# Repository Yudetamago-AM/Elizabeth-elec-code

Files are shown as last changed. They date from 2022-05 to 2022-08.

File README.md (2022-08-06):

# CanSat2022

この文書をソフト全体のドキュメントとして扱えるようにしたいなーと思っています．

## 注意
プログラムを書く前に，VS Codeのソース管理タブ→三点リーダ，レポジトリからプルすること．

## はじめに

ここでは，第18回能代宇宙イベントに向けた缶サットのプログラムを開発する．なお，われわれの缶サットの成功基準は下のように定められている．

| 種別 | 基準 |
| ---- | ---- |
| Minimum Success | 機体の損傷無く着地し，パラシュートを切り離す．制御履歴を保存する． |
| Full Success | 正常な動作を開始し，ゴール5m圏内に近づく． |
| Extra Success | ゴール0mまで近づき停止する． |

## 本番の流れ

1. 前日にゴール場所の座標を調べる．
1. 当日投下前に，動作タイマーをセットする．
1. 投下→自動誘導
この中で使うプログラムをここで書いていく．

## 回路について

### 搭載部品

主要な搭載部品は以下の通りである．

| 役割 | 型番 | 参考になるサイト |
| --- | --- | --- |
| マイコン | ATmega328P | <https://ht-deko.com/arduino/atmega328p.html> |
| GNSS | AE-GYSFDMAXB | <https://github.com/askn37/GPS_MTK333X> |
| 9軸センサー | AE-BNO055-BO | <https://learn.adafruit.com/adafruit-bno055-absolute-orientation-sensor/arduino-code> |
| 超音波距離センサー | HC-SR04 | <https://akizukidenshi.com/catalog/g/gM-11009/> |
| microSD | AE-microSD-LLCNV | <https://akizukidenshi.com/catalog/g/gK-14015/> |
| モータードライバ | TB67H450FNG | <https://www.marutsu.co.jp/contents/shop/marutsu/datasheet/TB67H450FNG.pdf> |

なお，マイコンと部品間のピンアサインは，PinAssign.hを参照．

## 実装上の注意

メモリが限られている（全体で2048バイト，SDカードのバッファ用に512バイト，Arduino Bootloaderにいくらか持って行かれている）ため，メモリを節約してプログラムを書くこと．

## 必要なライブラリ

### モーター制御

がんばって書く，TB67H450FNGを用いたPWM定電流制御．電流値は，基板上の抵抗で決める．
前進，後進，ブレーキ，超信地旋回ができるように．早さはPWMで指定して呼び出す感じにする．
PWMは100以上くらいじゃないと，うまく回らない印象（実際に使うモーターでなくて，マブチモーターだけど）．あと，回り始めに一気に電流が必要そうなので，コンデンサの容量増やしたりした方が良いかも．

### GNSS情報取得

<https://github.com/askn37/GPS_MTK333X>
このなんだか便利（シンプル）そうなライブラリが使えそうです．なので，ちょちょっとメイン制御の方に書くのみで大丈夫と思います．

### ログ記録

AE-microSD-LLCNVを使う．がんばって書く．そんなに大変そうじゃ無い．

### 9軸

方位，加速度などを取得する．秋月のBNO055採用のため，Adafruitのライブラリが使える．
方位の値が安定しない問題があったが，SDAに2.2K, SCLに3.3Kのプルアップ抵抗を付けることで解決する（詳細はAdafruit BNO055のFAQを参照）．
→組み立て時に追加する．
また，信頼できる値は，bno.getCalibration(引数)の相当する引数の値が，0でない時である．

## メインプログラム

### メイン制御 [Main.ino]

各Seqをそれぞれ呼び出す．

### Landing()

- 着地判定
9軸の加速度の大きさ，（GPSの速度の大きさを見る），念のためタイマーも入れておく．
- パラシュートに絡まないようにする（すこし前に進む？）．
- ニクロム線カット
PIN_NICHROME(中身はanalog pin 7(PD7))をHIGHにすればオンになるはず．

#### ニクロム線溶断について

実験してみたところ，ニクロム線が短すぎると，バッテリの短絡防止回路がうごいて，モーター・ニクロム線系統の電源が落ちてしまう．
ニクロム線を長めに取る（5Ω分くらい）と，うまくいく（抵抗を付けるのもありかも→要実験）．
溶断にかかる時間は，ある程度テンションをかけた状態で，3秒ほどであった．
このため，ニクロム線の長さにもよるが，5秒ほど電流を流した方が良いかと思う．

### GuideGPS()

- GPSで精度限界まで誘導する
上に上げたライブラリを叩いて今の座標とか取得して良い感じに計算して誘導すれば良いはず．

今更気付いたのだが，Arduinoのfloat型は"the total number of digits"で6-7桁しか精度がないため，目的地への角度・距離の計算結果には十分な精度がない（というのも，緯度・経度は小数点以下6桁でおよそ10cm精度が出るためであり，われわれにはこのくらい必要だからである）．
困ったので，GPSの座標は固定小数点として扱う．

### GuideDIST()

- 超音波距離センサーで0mまで誘導する

われわれはついてるはずなので，カラーコーン±50cmくらいまでGPSで誘導できるはず．その後，超信地旋回をしながら，カラーコーンの位置と距離を認識して，その距離分進む．

### Goal()

ゴール判定をする．ゴールと判定したら，プログラム終了！
GuideDIST()でむしろ明後日の方向へ行ってしまっているようならば，もういちどGPSで誘導して終わりにする．

### Distance()

超音波距離センサーをつかって，目の前の物体までの距離をcmで返す．
（一応，九軸センサー内の温度センサーをつかって音速を校正しているが，逆に安定性を損なうようだったら，→board tempなのか…ならばつかえないのか）20℃1気圧とかで計算しておく．

### タイマー [Main.ino]

あらかじめ設定してあるタイマー（int Timer）(ms)と，millis()を比較する．
（millis()はプログラム開始からの時間をmsで返す）（<http://www.musashinodenpa.com/arduino/ref/index.php?f=0&pos=2524>）

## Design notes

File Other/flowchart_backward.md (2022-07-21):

#
```flow

start=>start: 開始
end=>end: 終了

getrad=>operation: 機体のピッチ取得
forward=>operation: モーター制御
（前転）
isbackward=>condition: 機体が
反転しているか
log=>operation: ログ書き込み

start->getrad(right)->isbackward(no, bottom)->log(right)->end
isbackward(yes)->forward(right)->log

```

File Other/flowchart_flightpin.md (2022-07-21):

```flow

start=>start: 開始
end=>end: 終了

flightpin=>condition: フライトピン

```

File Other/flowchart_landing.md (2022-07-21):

```flow

start=>start: 開始
end=>end: 終了
flightPin=>condition: フライトピン解放
からの時間 > 40(s)
timer=>condition: 電源投入からの
時間 > 600(s)
cutting=>subroutine: テグス溶断
log=>operation: ログ書き込み
phase=>operation: フェーズ=GPS誘導フェーズ

start->flightPin(yes)->cutting
flightPin(no)->timer
timer(no)->flightPin()
timer(yes)->cutting(right)->log(right)->phase->end

```

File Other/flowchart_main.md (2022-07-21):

```flow

start=>start: 開始
end=>end: 終了
wait=>subroutine: フライトピン
landing=>subroutine: 着地時動作
gpsGuide=>subroutine: GPS誘導
distGuide=>subroutine: 精密誘導
isGoal=>condition: ゴール判定
timesCalled=>condition: 呼出回数 < 3
 
start->wait->landing->gpsGuide->timesCalled

```

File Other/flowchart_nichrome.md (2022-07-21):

##

```flow

start=>start: 開始
end=>end: 終了
Nichrome=>operation: ニクロム線加熱
（テグス溶断）
forward=>operation: モーター制御
（前進）

start(right)->Nichrome(right)->forward(right)->end

```

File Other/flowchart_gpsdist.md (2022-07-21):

```flow

start=>start: 開始
end=>end: 終了
backward=>subroutine: 機体の反転検出・修正
rotate90=>operation: 90度左旋回
rotate=>operation: 10度右旋回
checkdist=>inputoutput: 前方の距離確認
ischecked=>condition: 物体検知したか
rotatedir=>operation: 物体の方向へ旋回
forward=>operation: モーター制御
（直進）
log=>operation: ログ書き込み
isgoal=>operation: フェーズ=ゴール判定フェーズ

start->backward->rotate90->checkdist->rotate->ischecked
ischecked(yes)->rotatedir->forward->log->isgoal->end
ischecked(no)->checkdist

```

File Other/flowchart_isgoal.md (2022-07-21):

```flow

start=>start: 開始
end=>end: 終了
end2=>end: 終了

backward=>subroutine: 機体の反転検出・修正
gpscheck=>operation: ゴールまでの距離・方位取得
dist400=>condition: ゴールまでの
距離 < 400(cm)
goalcount=>condition: ゴール判定の
呼出回数 < 5
distfor=>inputoutput: 機体前側の距離取得
distfor2=>inputoutput: 機体前側の距離取得
rotate=>operation: 小旋回
phasegps=>operation: フェーズ=GPS誘導
phasedist=>operation: フェーズ=精密誘導
phase5=>operation: フェーズ=回収まで待機
phase5b=>operation: フェーズ=回収まで待機
log=>operation: ログ書き込み
log2=>operation: ログ書き込み
check=>condition: 距離 < 12(cm)
calcgps=>subroutine: ゴールへの方位・距離計算

start(right)->backward(right)->calcgps->dist400
dist400(no)->goalcount
dist400(yes, right)->phasegps->phase5->log->end2
goalcount(no)->phasegps
goalcount(yes, right)->distfor->check
check(yes)->log2->phase5b->end
check(no)->phasedist->phase5b

```

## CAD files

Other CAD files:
Experiments/PlainC_gpsCalc/GPScalc.obj

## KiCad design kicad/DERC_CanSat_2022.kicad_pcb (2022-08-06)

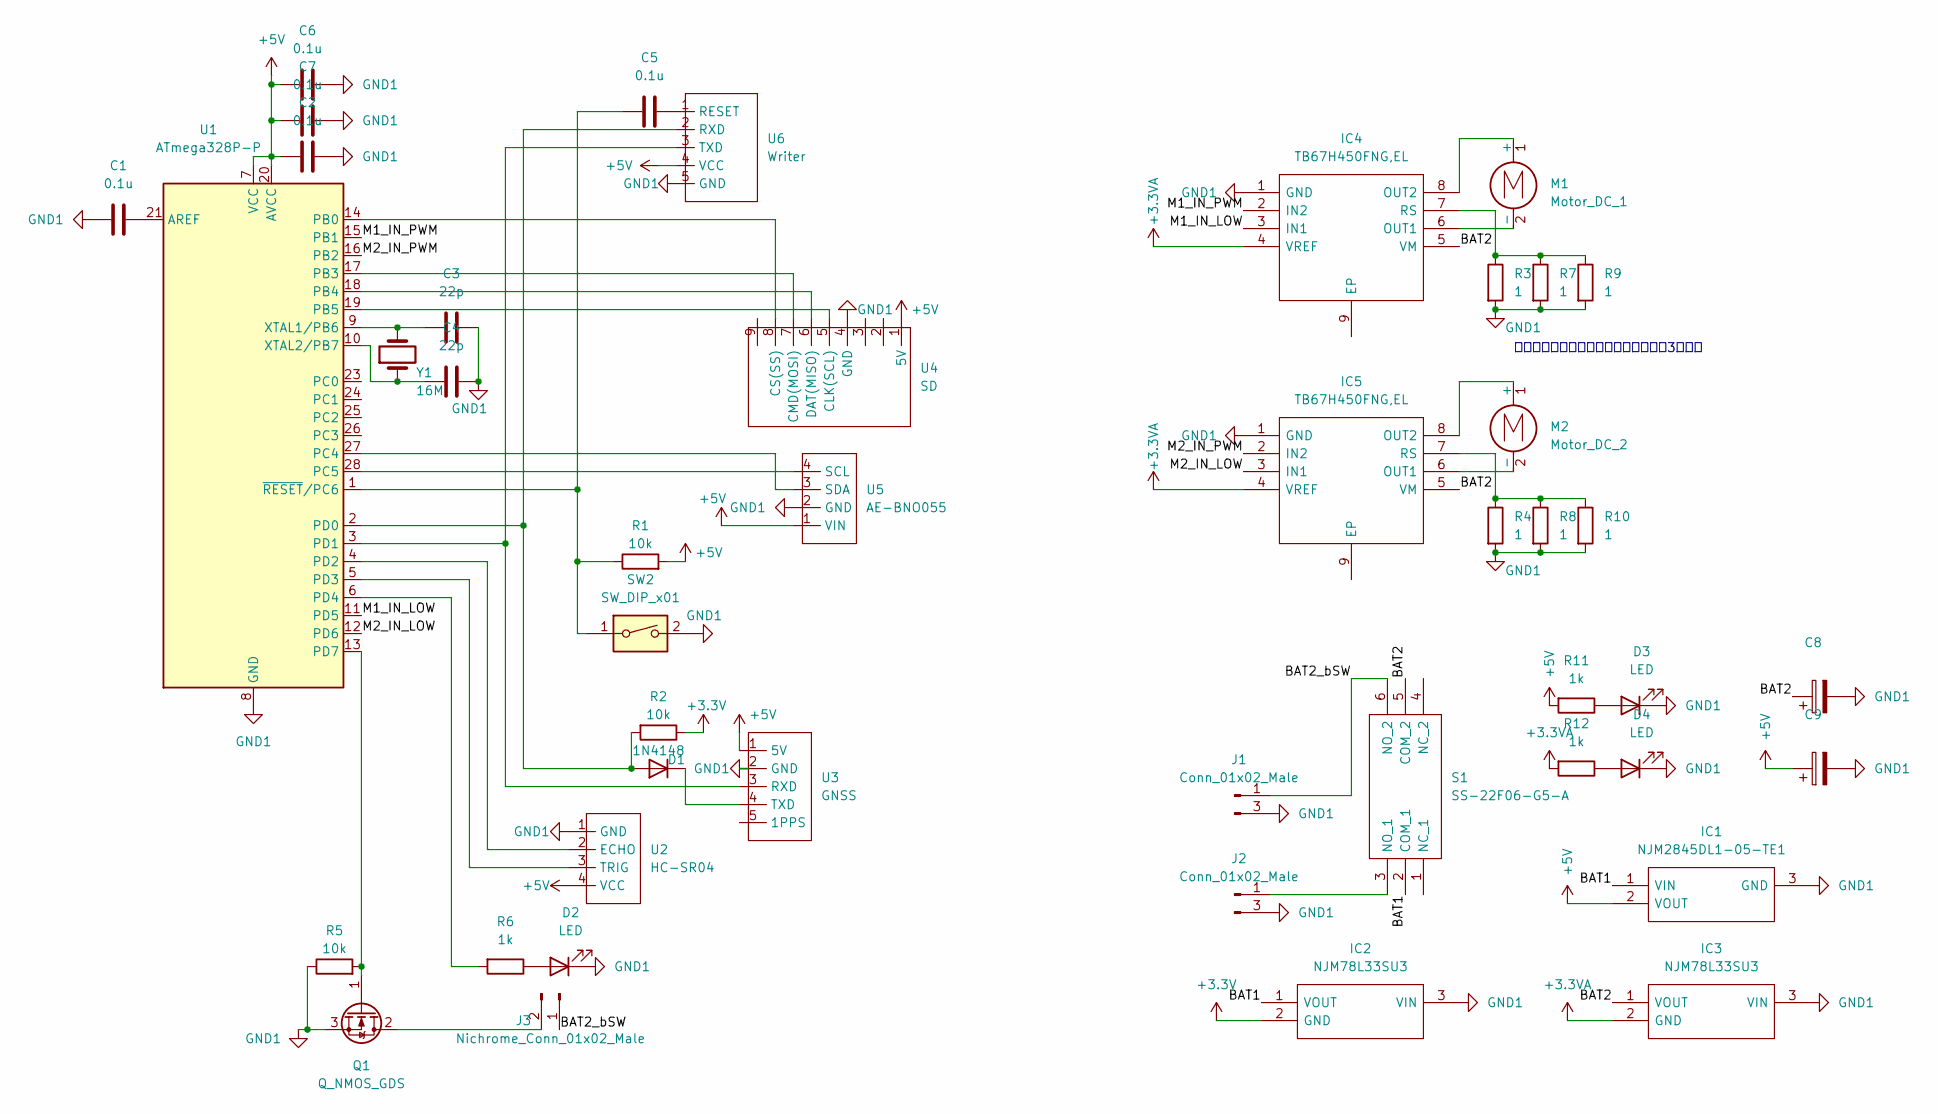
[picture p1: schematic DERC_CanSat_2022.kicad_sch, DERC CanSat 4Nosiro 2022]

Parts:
C1, C2, C5, C6, C7: 0.1u; C_Disc_D3.0mm_W1.6mm_P2.50mm
C3, C4: 22p; C_Disc_D3.0mm_W1.6mm_P2.50mm
C8, C9: (no value)
D1: 1N4148; D_DO-35_SOD27_P7.62mm_Horizontal
D2, D3, D4: LED; LED_D3.0mm
IC1: NJM2845DL1-05-TE1; TO-252-2; Manufacturer_Part_Number NJM2845DL1-05-TE1
IC2, IC3: NJM78L33SU3; SOT-89-3; Manufacturer_Part_Number NJM78L33SU3
IC4, IC5: TB67H450FNG,EL; SOIC127P600X175-9N; Manufacturer_Part_Number TB67H450FNG,EL
J1, J2: Conn_01x02_Male; JST_PH_B3B-PH-K_1x03_P2.00mm_Vertical
J3: Nichrome_Conn_01x02_Male; TerminalBlock_Altech_AK300-2_P5.00mm
M1: Motor_DC_1; JST_XH_B2B-XH-A_1x02_P2.50mm_Vertical
M2: Motor_DC_2; JST_XH_B2B-XH-A_1x02_P2.50mm_Vertical
Q1: Q_NMOS_GDS; TO229P241X654X988-3P
R1, R2, R5: 10k; R_Axial_DIN0207_L6.3mm_D2.5mm_P7.62mm_Horizontal
R3, R4, R7, R8, R9, R10: 1; R_Axial_DIN0207_L6.3mm_D2.5mm_P2.54mm_Vertical
R6, R11, R12: 1k; R_Axial_DIN0207_L6.3mm_D2.5mm_P7.62mm_Horizontal
S1: SS-22F06-G5-A; PowerSwitch; Manufacturer_Part_Number SS-22F06-G5-A
SW2: SW_DIP_x01; TVBP06B043CWB
U1: ATmega328P-P; DIP-28_W7.62mm
U2: HC-SR04
U3: GNSS
U4: SD
U5: AE-BNO055
U6: Writer; PinHeader_1x05_P2.54mm_Vertical
Y1: 16M; Crystal_HC49-4H_Vertical

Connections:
+3.3VA: IC3.2 (GND), IC4.4 (VREF), IC5.4 (VREF), R12.2
+3V3: IC2.2 (GND), R2.1
+5V: C2.1, C6.1, C7.1, C9.1, IC1.2 (VOUT), R1.2, R11.2, U1.7 (VCC), U1.20 (AVCC), U2.4 (VCC), U3.1 (5V), U4.1 (5V), U5.1 (VIN), U6.4 (VCC)
/BAT1: IC1.1 (VIN), IC2.1 (VOUT), S1.2 (COM_1)
/BAT2: C8.1, IC3.1 (VOUT), IC4.5 (VM), IC5.5 (VM), S1.5 (COM_2)
/BAT2_bSW: J1.1, J3.1, S1.6 (NO_2)
/M1_IN_LOW: IC4.3 (IN1), U1.11 (PD5)
/M1_IN_PWM: IC4.2 (IN2), U1.15 (PB1)
/M2_IN_LOW: IC5.3 (IN1), U1.12 (PD6)
/M2_IN_PWM: IC5.2 (IN2), U1.16 (PB2)
GND1: C1.1, C2.2, C3.2, C4.2, C6.2, C7.2, C8.2, C9.2, D2.1 (K), D3.1 (K), D4.1 (K), IC1.3 (GND), IC2.3 (VIN), IC3.3 (VIN), IC4.1 (GND), IC5.1 (GND), J1.3 (Pin_2), J2.3 (Pin_2), Q1.3 (S), R3.2, R4.2, R5.1, R7.2, R8.2, R9.2, R10.2, SW2.2, U1.8 (GND), U1.22 (GND), U2.1 (GND), U3.2 (GND), U4.4 (GND), U5.2 (GND), U5.6, U6.5 (GND)
unnamed: C1.2, U1.21 (AREF)
unnamed: C3.1, U1.9 (XTAL1/PB6), Y1.2
unnamed: C4.1, U1.10 (XTAL2/PB7), Y1.1
unnamed: C5.1, R1.1, SW2.1, U1.1 (~RESET/PC6)
unnamed: C5.2, U6.1 (RESET)
unnamed: D1.1 (K), U3.4 (TXD)
unnamed: D1.2 (A), R2.2, U1.2 (PD0), U6.2 (RXD)
unnamed: D2.2 (A), R6.1
unnamed: D3.2 (A), R11.1
unnamed: D4.2 (A), R12.1
unnamed: IC4.6 (OUT1), M1.2 (-)
unnamed: IC4.7 (RS), R3.1, R7.1, R9.1
unnamed: IC4.8 (OUT2), M1.1 (+)
unnamed: IC5.6 (OUT1), M2.2 (-)
unnamed: IC5.7 (RS), R4.1, R8.1, R10.1
unnamed: IC5.8 (OUT2), M2.1 (+)
unnamed: J2.1, S1.3 (NO_1)
unnamed: J3.2, Q1.2 (D)
unnamed: Q1.1 (G), R5.2, U1.13 (PD7)
unnamed: R6.2, U1.6 (PD4)
unnamed: U1.3 (PD1), U3.3 (RXD), U6.3 (TXD)
unnamed: U1.4 (PD2), U2.2 (ECHO)
unnamed: U1.5 (PD3), U2.3 (TRIG)
unnamed: U1.14 (PB0), U4.8 (CS(SS))
unnamed: U1.17 (PB3), U4.7 (CMD(MOSI))
unnamed: U1.18 (PB4), U4.6 (DAT(MISO))
unnamed: U1.19 (PB5), U4.5 (CLK(SCL))
unnamed: U1.27 (PC4), U5.3 (SDA)
unnamed: U1.28 (PC5), U5.4 (SCL)

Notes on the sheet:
抵抗値で定電流制御の電流決めるため3本パラ

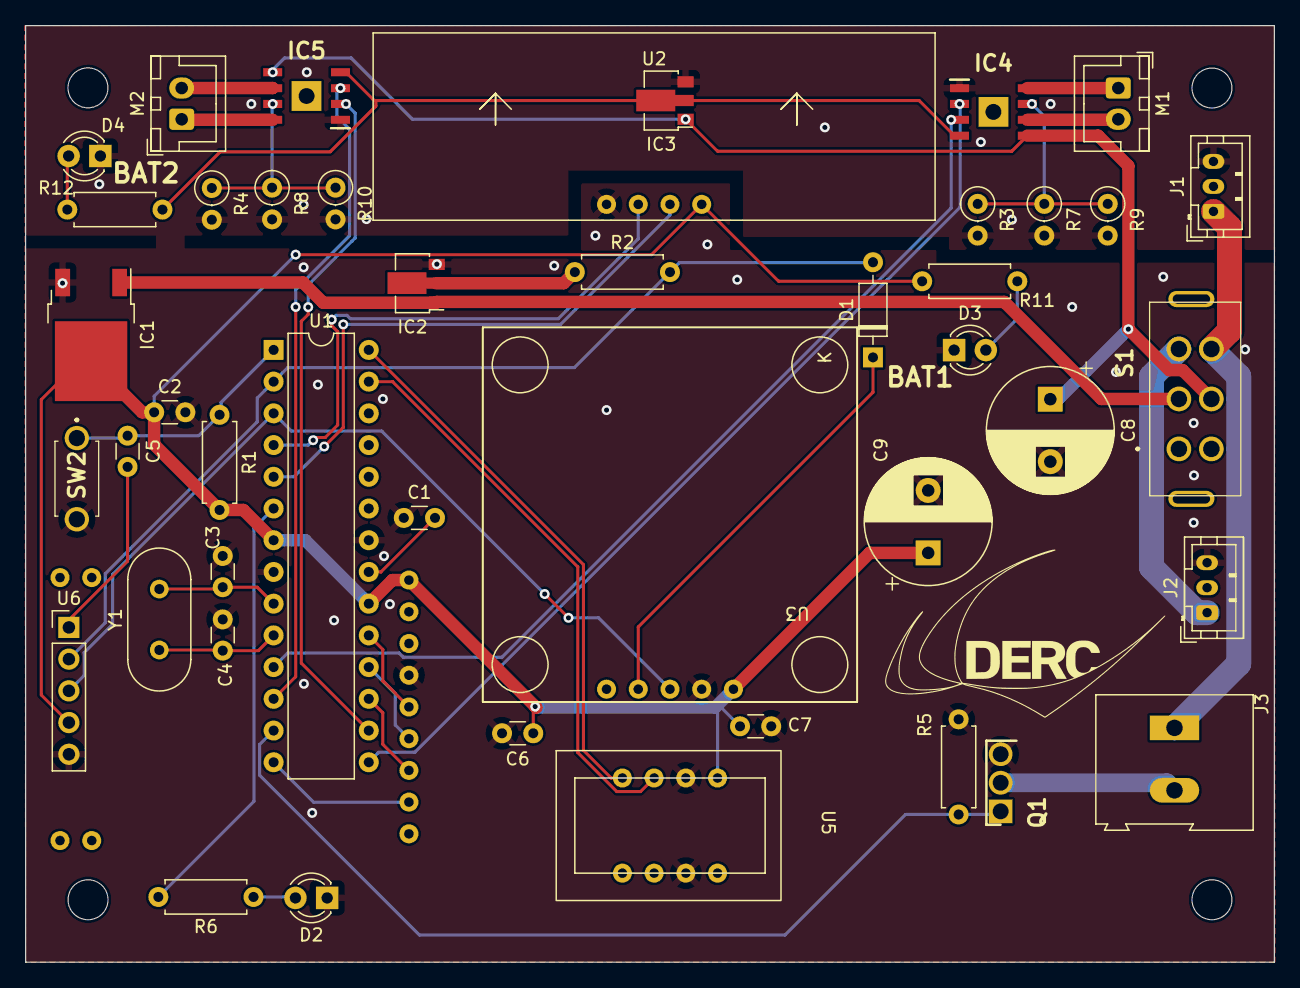
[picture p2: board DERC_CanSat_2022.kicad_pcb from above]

Board: 2 copper layers, 100.0 x 75.0 mm, 46 parts (1 on the bottom side), 40 nets.

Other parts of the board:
2022: LOGO; logotekina_25

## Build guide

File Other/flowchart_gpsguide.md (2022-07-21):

```flow

start=>start: 開始
end=>end: 終了

backward=>subroutine: 機体の反転検出・修正
getgps=>inputoutput: GPS座標取得
getrad=>inputoutput: 機体の方位取得
calcgps=>subroutine: ゴールへの方位・距離計算
rotate=>operation: モーター制御（旋回）
log=>operation: ログ書き込み
isdone=>condition: ゴールまでの
距離 < 3m
phase=>operation: フェーズ=精密誘導フェーズ

start->backward->calcgps()->rotate->log->isdone
isdone(yes, right)->phase->end
isdone(no)->end

```

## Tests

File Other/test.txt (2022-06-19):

set datafile separator ","
set yrange [-40: 40]
set xlabel "Time (ms)"
set ylabel "Accel (m/s^2)"
plot "L14.dat" using 1:2 w lp title "X-axis"
replot "L14.dat" using 1:3 w lp title "Y-axis"
replot "L14.dat" using 1:4 w lp title "Z-axis"

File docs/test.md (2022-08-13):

# テスト

これはテストファイルです．

>We look before and after  \
>　　And pine for what is not:  \
>Our sincerest laughter  \
>　　With some pain is fraught;  \
>Our sweetest songs are those that tell of saddest thought.

>「前をみては、後えを見ては、物欲しと、あこがるるかなわれ。腹からの、笑といえど、苦しみの、そこにあるべし。うつくしき、極の歌に、悲しさの、極みの想、籠るとぞ知れ」

（夏目漱石『草枕』より．
青空文庫：<https://www.aozora.gr.jp/cards/000148/files/776_14941.html>）

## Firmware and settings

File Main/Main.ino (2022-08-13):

/*
あらかじめ，
https://github.com/askn37/Futilities
https://github.com/askn37/GPS_MTK333X
https://github.com/adafruit/Adafruit_Sensor
https://github.com/adafruit/Adafruit_BusIO
https://github.com/adafruit/Adafruit_BNO055
をライブラリに読み込んでおくこと．
*/

#include <Arduino.h>
#include <Wire.h>
#include <SoftwareSerial.h>
#include <GPS_MTK333X_SoftwareSerial.h>
//#include <GPS_MTK333X_Serial.h>
#include <Adafruit_Sensor.h>
#include <Adafruit_BNO055.h>
#include <utility/imumaths.h>
/*以下lib内自作ライブラリ*/
#include <PinAssign.h>
#include <Motor.h>
#include <SD_RW.h>

#define ANGLE_TH 0.39//前45度，GPS誘導
#define LONGITUDE_PER_RES 141//能代
#define LATITUDE_PER_RES 185

byte phase = 0;
/*重要！！電源オンからのタイマー，ミリ秒単位で指定*/
const unsigned long Timer = 600000; //600 * 1000, 600秒 は 10分
/*フライトピン解放からのタイマー*/
const unsigned int flightPinTimer = 10000;//50s//10s
unsigned long flightPinMillis;
/*重要！！ゴールのGPS座標*/
const long goal_longitude = 84082711; //経度*600000(60万)
const long goal_latitude = 24135694; //緯度*600000

bool isFirstUnplug = true;
bool isFirstDIST = false;
byte goalCount = 0;

GPS_MTK333X_SoftwareSerial GPS(PIN_GPS_RX, PIN_GPS_TX);
//GPS_MTK333X_Serial GPS;
Adafruit_BNO055 bno = Adafruit_BNO055(55, 0x28);

void setup() {
    /*Motor initialize*/
    motor_init();
    motor_stop();

    /*ニクロム線の初期設定*/
    pinMode(PIN_NICHROME, OUTPUT);
    digitalWrite(PIN_NICHROME, LOW);

    /*//Serial (for debug) initialize*/
    Serial.begin(9600);
    Serial.println(F("Serial begin"));

    /*FOR DEBUG!! mem check*/
    /*不要なときはコメントアウト！！*/
    // 5/16時点で723bytesあまってる感じ
    /*
    //Serial.print(F("Free memory="));
    //Serial.print(freeRam(), DEC);
    //Serial.println(F("[bytes]"));
    */

    /*SD initialize*/
    sd_init();

    /*BNO055 initialize*/
    while (!bno.begin()) {
        //Serial.println(F("BNO055 not ready"));
        delay(100);
    }
    bno.setExtCrystalUse(true);//のっかってるからには使わねば（精度向上）
    //Serial.println(F("BNO055 ready"));

    /*GPS initialize*/
    while (!GPS.begin(9600)) {
        //Serial.println(F("GPS not ready"));
        delay(100);
    }
    // UARTボーレートを 9600bpsに設定する
    GPS.sendMTKcommand(251, F(",9600"));
    // 1000ms間隔で NMEAを出力する
    GPS.sendMTKcommand(220, F(",1000"));
    //GPS.sendMTKcommand(300, F(",1000,0,0,0,0"));
    // AlwaysLocate モード開始 
    //GPS.sendMTKcommand(225, F(",8"));
    // 上記を解除してスタンダードモードに遷移
    GPS.sendMTKcommand(225, F(",0"));
    // QZSS（みちびき）をサポートする
    GPS.sendMTKcommand(351, F(",1"));
    // RMCとGGAをともに1サイクルで出力する（1サイクル時間は PMTK220 による）
    // 各項は ",GLL,RMC,VTG,GGA,GSA,GSV,0,0,0,0,0,0,0,0,0,0,0,ZDA,MCHN"
    GPS.sendMTKcommand(314, F(",0,1,0,1,0,0,0,0,0,0,0,0,0,0,0,0,0,0,0"));
    //Serial.println(F("GPS ready"));

    /*Distance sensor initialize*/
    pinMode(PIN_DIST_TRIG, OUTPUT);
    pinMode(PIN_DIST_ECHO, INPUT);
    digitalWrite(PIN_DIST_TRIG, LOW);

    /*flight pin initialize*/
    pinMode(PIN_FLIGHT, INPUT);

    //4debug
    //Serial.println(F("setup done!"));
    sd_log(F("State,Decision,Control"));//S: State, D: Decision, C: Control, R: Result
    sd_log(F("Init done!"));
    sd_log("G_lat:" + String(goal_latitude));
    sd_log("G_long:" + String(goal_longitude));
    //getGPS(NULL, NULL);
    delay(50);
}

void loop() {
    //GPS受信バッファあふれ防止→たぶん不要？（ちゃんと見に行くから）
    //GPS.check();
    switch (phase) {
    case 0://パラシュート展開まで待つ
        waitTilUnPlug();
        break;
    case 1:
        Landing();
        break;
    case 2:
        GuideGPS();
        //stack();
        break;
    case 3:
        //Backward();
        GuideDIST();
        //stack();
        break;
    case 4:
        //Backward();
        Goal();
        //stack();
        break;
    case 5://ゴール後
        GPS.check();
        delay(10000);
        break;
    }
}

/*各シークエンス*/
void waitTilUnPlug() {
    Serial.println(F("wait"));
    //フライトピン
    if ((digitalRead(PIN_FLIGHT) == HIGH) && isFirstUnplug) {
        flightPinMillis = millis();
        isFirstUnplug = false;
        //Serial.println(F("pin ms set!"));
        sd_log(F("F_Pin:removed"));
        phase = 1;//landing
        BnoGetCal();
    } else if (Timer <= millis()) {
        phase = 1;
    }
    delay(50);
    return;
}

void Landing() {
    Serial.println(F("land"));
    //Serial.println(F("Landing seq begin"));
    //if (millis() <= flightPinMillis + flightPinTimer) return;
    if (((flightPinMillis + flightPinTimer) <= millis())) {
        sd_log(F(",F_Pin:landed"));
        // 前にうごかしたりパラシュート切り離したり…
        /*ニクロム線のカット*/
        Nichrome();
    } else if (Timer <= millis()){
        sd_log(F(",Timer:landed"));
        // 前にうごかしたりパラシュート切り離したり…
        /*ニクロム線のカット*/
        Nichrome();
    }

    BnoGetCal();
    //Serial.println(F("done"));
}

void BnoGetCal() {
    //センサーのキャリブレーションしとく
    byte mag;
    for (byte i = 0; i < 100; i++) {
        bno.getCalibration(NULL, NULL, NULL, &mag);
        delay(10);
        if (mag > 0) break;
    }
    return;
}

void Nichrome(){
        Serial.println(F("nic"));
        digitalWrite(PIN_NICHROME, HIGH);
        delay(2000);
        motor_forward(255, 255);
        delay(3000);
        digitalWrite(PIN_NICHROME,LOW);
        motor_stop();
        sd_log(F(",,Nichrome heat"));
        phase = 2;//gps
}

/*guide to the goal using GPS*/
void GuideGPS() {
    Serial.println(F("gps"));
    //Serial.println(F("gidG bgn"));
    sd_log(F("GPS Guide"));
    //方位・距離を計算
    double direction, distance, angle;//方位，距離，角度の差
    imu::Vector<3> e_orientation_now;

    getGPS(&direction, &distance);
    sd_log("dir:" + String(direction));
    sd_log("dist:" + String(distance));

    //ゴールまでgpsで2.5m以内なら，精密誘導へ
    if (distance <= 300) {//1.5 * 100 * 600000，あってるかわからない
        motor_stop();
        phase = 3;//guideDIST
        sd_log(F(",GPS Guide done"));
        return;
    }
    
    //if (distance <= 600) ANGLE_TH = 0.2;//左右各12度，全部で24度
    //方位をみて制御
    getRad(&e_orientation_now);
    //angle = e_orientation_now.x() - direction;

    //bool isPlus = false; //trueなら正，falseなら負
    //if (angle > 0) isPlus = true;
    
    //if (direction > 0) angle = direction + e_orientation_now.x();
    //else angle = direction - e_orientation_now.x();
    
    angle = direction + e_orientation_now.x();

    while (angle > PI_FLOAT) {
        angle -= PI_FLOAT;
    }
    while (angle < ((-1) * PI_FLOAT)) {
        angle += PI_FLOAT;
    }
    /*
    sd_log(",goal or:" + String(angle) + ",,");

    if (angle <= 0.26 && angle >= -0.26) {
        motor_forward(255, 255);//だいたい15度, 3.15-0.26
        sd_log(",,m_f:2525,");
    } else if (angle <= 1.3) {
        motor_forward(178, 255);//だいたい75度，ゴールが右手，出70%くらい
        sd_log(",,m_f:1725");
    } else if (angle >= -1.3) {
        motor_forward(255, 178);
        sd_log(",,m_f:2517");
    } else if (angle >= 0) {
        motor_forward(76, 255);
        sd_log(",,m_f:0725");
    } else if (angle <= 0) {
        motor_forward(255, 76);//わざと3.15，というのも，PI = 3.141592...で，3.14ならカバーできない角度が生まれるため
        sd_log(",,m_f:2507");
    }
    */

    //パターン2
    if ((angle > ((-1) * ANGLE_TH)) && (angle < ANGLE_TH)) {
        motor_forward(255, 255);
        sd_log(",diff:" + String(angle));
        sd_log(F(",,m_f:255255"));
        delay(900);
    } else {
        motor_rotate_L(255);
        delay(200);
        motor_stop();
        rotate((-1) * direction);
        sd_log(",rotate to:" + String((-1) * direction));
        motor_stop();
    }
    //delay(800);

    //delay(2000);
    //delayしなくても，1Hzくらいではうごくはず．→うごいた

    //Serial.println(F("done"));
    return;
}

void GuideDIST() {
    //Serial.println(F("gidD bgn"));
    if (isFirstDIST == true) {
        motor_forward(255, 255);
        delay(2000);
        motor_stop();
        isFirstDIST = false;
    }
    /*精密誘導が上手くいかない場合*/
    if (goalCount > 4) {
        phase = 5;
        return;
    }

    sd_log(F("DIST Guide"));
    imu::Vector<3> e_orientation_now;
    getRad(&e_orientation_now);

    byte dist[18], i;//あるいは，印付けてみるとか？
    dist[0] = 200;
    rotate(e_orientation_now.x() - 1.57);//90度左回転
    
    for (i = 0; i < 18; i++) {
        getRad(&e_orientation_now);
        dist[i] = Distance() / 2;//2cm単位 
        rotate(e_orientation_now.x() + 0.175);
        delay(10);
        /*
        for ((dist[i] < 200) && (abs(dist[i] - dist[i - 1]) > 100)) {
            sd_log("dist:" + String(dist[i]))
        }
        */
    }

    for (i = 0; i < 18; i++) {
        if((dist[i] < 200) && (abs(dist[i] - dist[i - 1]) < 10)) {
            //ログ
            sd_log("dist_num:" + String(i));//distance direction
            sd_log("dist:" + String(dist[i]));

            //制御
            getRad(&e_orientation_now);
            rotate(e_orientation_now.x() - (0.175 * (18 - i)));
            delay(10);
            //millisTemp2 = millis();
            sd_log(F(",,m_f:255255"));
            motor_forward(255, 255);
            delay(850);
            /*
            while (1) {
                if (millisTemp2 + 1500 <= millis()) {
                    motor_stop;
                    break;
                }
            }
            */
            break;
        }
    }

    //Serial.println(F("done"));
    phase = 4;//is goal?
}

void Goal() {
    //Serial.println(F("isGoal begin"));
    sd_log(F("isGoal"));

    bool gpsComplete = false;
    bool right = false, left = false;
    double direction, distance;

    getGPS(&direction, &distance);
    if (distance < 400) {//gpsで5m以内
        gpsComplete = true;
    } else if (goalCount > 4) {
        phase = 2;
        return;
    }

    //0m判定
    if (gpsComplete && (Distance() < 5)) {
        motor_rotate_R(100);
        delay(200);
        motor_stop();
        if (Distance() < 5) right = true;

        motor_rotate_L(100);
        delay(200);
        motor_stop();
        if (Distance() < 5) left = true;
    } else {
        phase = 4;
    }
    if (gpsComplete && right && left) {
        phase = 5;//guide done -- wait for power off
        //Serial.println(F("0m goal!"));
    }
    goalCount++;
    return;
}

void Backward() {
    imu::Vector<3> e_orientation_now;
    getRad(&e_orientation_now);
    sd_log("or_y:" + String(e_orientation_now.y()));
    sd_log(F(",,m_f:178178"));

    while (!((e_orientation_now.z() > -0.3) && (e_orientation_now.z() < 0.3))) {//あとで閾値設定  
        motor_forward(178, 178);
        getRad(&e_orientation_now);
    }
    motor_stop();
    
    return;
}

/*Landing用
bool isLanded() {
    bool isLanded = false;
    //フライトピンが加わったから，そのため書き直す
    if (Timer <= millis()) isLanded = true;
    else if (!isMoving()) isLanded = true;
    
    return isLanded;
}
*/

/*GPSで方位と距離を計算する
double getGPS(double* direction, double* distance, imu::Vector<3>* e_orientation_now) {
    const unsigned long R = 6376008;//能代市役所から，地球の中心までの距離

    if (GPS.check() && GPS.isLocationUpdate()) {
        double dx, dy;//x, yの変位
        double longitude = GPS.longitude();
        double latitude = GPS.latitude();
        //計算
        dx = R * (goal_longitude - (longitude / 600000.0)) * cos(goal_latitude);
        dy = R * (goal_latitude - (latitude / 600000.0));
        *direction = atan2(dy, dx);
        *distance = sqrt(pow(dx, 2) + pow(dy, 2));
        //ログ
        sd_gpslog(GPS.time(), &longitude, &latitude, e_orientation_now.x())
        GPS.statusReset();
    }
}
*/
/*GPSで方位と距離を計算する*/
double getGPS(double* direction, double* distance) {
    //const unsigned long R = 6376008;//能代市役所から，地球の中心までの距離
    unsigned long millisTemp;
    imu::Vector<3> e_orientation_now;

    //4debug
    //uint32_t start, end;

    while (true) {
        if (GPS.check() && GPS.isTimeUpdate() && GPS.isLocationUpdate()) {
        //Serial.println(F("gps updated (getGPS)"));
        //byte tri_goal_latitude = underbyte(goal_latitude);
        getRad(&e_orientation_now);
        sd_gpslog(String(GPS.longitude()), String(GPS.latitude()), String(e_orientation_now.x(), 4));

        //計算
        
        /*
        dx = R * (goal_longitude - GPS.longitude());// * long(cos(goal_latitude / 600000.0) * 100);
        //Serial.println(goal_longitude - GPS.longitude());
        //Serial.print(F("dx: "));
        //Serial.println(dx);
        
        dy = R * (goal_latitude - GPS.latitude());// * 100;
        //Serial.println(goal_latitude - GPS.latitude());
        //Serial.print(F("dy: "));
        //Serial.println(dy);
        */
        //x, yの変位
        long dx = ((goal_longitude - GPS.longitude()) * LONGITUDE_PER_RES);//0.000001度で0.092m(京田辺)，0.085m(能代)より，単位メートル
        long dy = ((goal_latitude - GPS.latitude()) * LATITUDE_PER_RES);//0.000001度で0.111m(111)より0.1
        
        if (dx == 0 && dy == 0) *direction = 0;
        else *direction = atan2(dx, dy);//意図的にdx, dyの順，というのも，北基準だから．
        *distance = approx_distance(dx, dy) / 10;//単位:cm
        //Serial.println(F("calc done (getGPS)"));
        //Serial.print(F("dir: "));
        //Serial.println(*direction);
        //Serial.print(F("dist: "));
        //Serial.println(*distance);

        //millisTemp = millis();
        //sd_log("dir:" + String(*direction));
        //while ((millisTemp + 5) < millis()) {}
        //sd_log("dist:" + String(*distance));

        //4debug
        //start = millis();
        //sd_log(",,," + String(GPS.longitude()) + "," + String(GPS.latitude()) + "," + String(e_orientation_now.x()));
        //sd_gpslog(String(GPS.longitude()), String(GPS.latitude()), String(e_orientation_now.x(), 4));
        //sd_gpslog(GPS.longitude() / 600000.0, GPS.latitude() / 600000.0, e_orientation_now.x());        
        //end = millis() - start;

        //Serial.print(F("sd write took(ms) : "));//およそ95msかかっていた
        //Serial.println(end);
        break;
        }
    }
    
    //Serial.println(F("gps logged!"));

}

/*平方根を使わず2点間の距離を近似*/
//参考
//https://nowokay.hatenablog.com/entry/20120604/1338773843
//https://dora.bk.tsukuba.ac.jp/~takeuchi/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
long approx_distance(long dx, long dy) {
   unsigned long min, max, approx;

   if (dx < 0) dx = -dx;
   if (dy < 0) dy = -dy;

   if (dx < dy) {
      min = dx;
      max = dy;
   } else {
      min = dy;
      max = dx;
   }

   approx = (max * 983) + (min * 407);
   if (max < (min << 4)) approx -= ( max * 40 );

   // add 512 for proper rounding
   return ((approx + 512) >> 10);
} 

/*その他
bool isMoving() {
    
    //動いていたらtrue，動いていなかったらfalseを返す
    //動いていないということは，すなわちスタックしている，ということではない．
    const int thAccel[3] = {1, 2, 1};// 動いているかどうかの閾値設定(m/s^2)　添字0:x軸, 1:y軸，2:z軸
    bool isMoving = false;
    sensors_event_t accelData;
    bno.getEvent(&accelData);

    if ((accelData.acceleration.x > thAccel[0]) && (accelData.acceleration.y > thAccel[1]) && (accelData.acceleration.z > thAccel[2])) {
        isMoving = true;
    }
    return isMoving;
}
*/

double Distance() {
    /*
    距離(cm)を返す
    一応，九軸センサー内蔵の温度センサーで温度を見て，校正しているが，だめっぽかったら15℃として計算してる
    これは, ambient temperature なのか， sensor temperatureなのか，よくわからん（データーシートにも混在）→実験してみる
    ！！メモリ節約のため，25度で計算
    */
    int Duration;
    double Distance;

    digitalWrite(PIN_DIST_TRIG, HIGH);
    delayMicroseconds(10);
    digitalWrite(PIN_DIST_TRIG, LOW);

    Duration = pulseIn(PIN_DIST_ECHO, HIGH, 23200);//400cm以上の場合0を返す
    if (Duration > 0) {
        //Distance = Duration * (0.6 * temp + 331.5) / 20000;
        // D(cm) = T(μS) × 1/2(片道) × 340(m/s) × 100(cm/m) × 1/1000000(μS/S)
        // https://nobita-rx7.hatenablog.com/entry/27884818
        // D = T * 0.00005 * c(m/s) = T / 20000
        // c(近似) = 0.6 * temp + 331.5　

        //Distance = Duration / 58.8;// 15℃ 1013hpa
        // D = T * 0.017 = T / 58.8

        Distance = Duration / 57.6;
        // 25度の音速346.75(m/s)なので347として計算
        // D = T * 0.01735 = T / 57.6
    } else {
        Distance = 400;
    }
    return Distance;
}

/*Rotate to the ABSOLUTE angle (in euler)*/
void rotate(double angle) {
    unsigned long millisTemp2 = 0;

    millisTemp2 = millis();
    /*
    PIN_MO_L/R_Bはそれぞれ5,6ピンを使っているので，デューティー比が若干高くなるそう（下リファレンス）．
    http://www.musashinodenpa.com/arduino/ref/index.php?f=0&pos=2153

    具体的には，5/6ピンから977Hz
    9/10ピンから490Hz
    3/11ピンから490Hzという3つがあり，490*2 = 980のためと思われる．
    （一応）その調整をする．
    */
    /*
    int offsetPWM = 1;//（およそ）1秒(50ms*20)に1回**offsetPWMの値**を引いたPWMでうごかす
    int count = 0;
    // メモリないのでやめにした
    */
    //いい感じに9軸センサー呼び出す感じ
    //cf1. https://learn.adafruit.com/adafruit-bno055-absolute-orientation-sensor/arduino-code
    //cf2. https://forums.adafruit.com/viewtopic.php?f=19&t=91723&p=462337#p462337
    /*
    ↑では，
    sensors_event_t rotate;
    bno.getEvent(&rotate);
    みたいに書いてあるが，
    https://learn.adafruit.com/using-the-adafruit-unified-sensor-driver/how-does-it-work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
    にあるように，Quternionはgeteventでは取得出来ない（=Raw Sensor Dataとして取得する必要がある）
    （なんのための"Unified" Sensor Systemだ？？，下手に使えんでないか）
    */
    //cf3. http://l52secondary.blog.fc2.com/blog-entry-50.html
    
    /*
    そのままEulerで取得するとpitch(y)かroll(x)軸が±45度を超えると，まともに使えるデータでなくなるから
    クォータニオンで値を取得してオイラー角に変換する
    ちなみに，（正）「クォータニオン」（誤）「クォータ二オン」，（誤）はニが2になってる，おのれATOK！
    */

    /*
    imu::Quaternion q_orientation_now = bno.getQuat();
    q_orientation_now.normalize();//重力分を取り除く（vector.h）
    */
    imu::Vector<3> e_orientation_now;
    getRad(&e_orientation_now);
    /*入れ替え
    // x to -y
    // y to x
    // z to -z
    double temp = q_orientation_now.x();
    q_orientation_now.x() = -q_orientation_now.y();
    q_orientation_now.y() = temp;
    q_orientation_now.z() = -q_orientation_now.z();
    //おそらく不要
    */
    /*
    imu::Vector<3> e_orientation_now = q_orientation_now.toEuler();
    double angleNow = radPI * e_orientation_now.z();
    */
    float destAngle;//destまでのangle
    if (angle > 0) destAngle = angle + e_orientation_now.x();
    else destAngle = angle - e_orientation_now.x();
    
    while (destAngle > 3.14) {
        destAngle -= 3.141592;
    }
    while (destAngle < -3.14) {
        destAngle += 3.141592;
    }
    //Serial.print(F("destAngle: "));
    //Serial.println(destAngle);
    /*旋回*/
    /*
    while (e_orientation_now.x() <= destAngle) {
        if (destAngle > 0) {
            motor_rotate_L(110);
            if ((e_orientation_now.x() <= destAngle) || dest)
        }
        else if (destAngle < 0) motor_rotate_R(110);

        if (millisTemp2 + 5000 <= millis()) {
            motor_stop();
            return;
        }

        delay(12);//9軸は100Hz=10msごと更新だが余裕を見る
        getRad(&e_orientation_now);
    }
    */
    
    if (destAngle > 0) {
        while (e_orientation_now.x() <= destAngle) {
            motor_rotate_L(255);
            sd_log(F(",,m_r_L:255"));
            
            if (millisTemp2 + 5000 <= millis()) break;
            delay(1);
            getRad(&e_orientation_now);
        }
        motor_rotate_R(255);
        delay(10);
        motor_stop();
        return;
    }
    if (destAngle < 0) {
        while (e_orientation_now.x() >= destAngle) {
            motor_rotate_R(255);
            sd_log(F(",,m_r_R:255"));
            
            if (millisTemp2 + 5000 <= millis()) break;
            delay(1);
            getRad(&e_orientation_now);
        }
        motor_rotate_L(255);
        delay(10);
        motor_stop();
        return;
    }
    
    return;
}


float getRad(imu::Vector<3>* e_orientation_now) {
    unsigned long millisTemp = 0;
    //止まっているとCalibrationが悪くなるので，だめだったらちょっと動かす用
    millisTemp = millis();

    uint8_t mag;//磁気センサーのキャリブレーション度を見る．
    imu::Quaternion q_orientation_now;
    
    do {
        bno.getCalibration(NULL, NULL, NULL, &mag);//system, gyro, accel, mag

        //for debug
        /*
        //Serial.print("system: ");
        //Serial.println(system);
        */
        q_orientation_now = bno.getQuat();
        
        
        if (millisTemp + 1000 < millis()) {
            motor_rotate_R(200);
            delay(300);
            motor_rotate_L(200);
            delay(300);
            motor_stop();
        }
        
    } while (mag < 1);//1, 2，3の時のみループを抜けて出力
    //一時的にすべての場合にしてみる
    
    q_orientation_now.normalize();//重力分を取り除く（vector.h）
    *e_orientation_now = q_orientation_now.toEuler();
}
/*
void stack() {
    if ((phase > 1) && isMoving) {
        //あとでちゃんと動くか確かめる
        imu::Vector<3> e_orientation_now;
        
        getRad(&e_orientation_now);
        while (e_orientation_now.y() < 0) {
            if (e_orientation_now.y() > 0.3) break;
            motor_forward(255, 255);
        }
        motor_stop();
    }
    
}
*/

/*FOR DEBUG!!*/
/*ローカル変数のメモリもみてみる*/
/*
int freeRam () {
  extern int __heap_start, *__brkval;
  int v;
  return (int) &v - (__brkval == 0 ? (int) &__heap_start : (int) __brkval);
}
*/

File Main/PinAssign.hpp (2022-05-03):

#ifndef PIN_ASSIGN
#define PIN_ASSIGN
/*
Arduinoブートローダであることを意識．
いちおう命名規則として，すべて大文字とする．

example:
digitalWrite(PIN_NICHROME, HIGH);
とすれば，digital pin 7がHIGHになります．
*/

/*
GPS
標準のI2Cバス（TX:0, RX:1）
*/

/*9軸センサー*/
/*
Adafruitのライブラリですでにdefineされてるはず
SDA A4
SCL A5
*/

/*距離センサー*/
#define PIN_DIST_ECHO 3
#define PIN_DIST_TRIG 4

/*SDカード*/
#define PIN_SD_CS 8
#define PIN_SD_CMD 11 //MOSI
#define PIN_SD_DATA 12 //MISO
#define PIN_SD_CLK 13 //SCL

/*右モーター(M1)*/
#define PIN_MO_R_PWM 9
#define PIN_MO_R_LOW 5

/*左モーター(M2)*/
#define PIN_MO_L_PWM 10
#define PIN_MO_L_LOW 6

/*インジケーターLED*/
#define PIN_LED 4

/*ニクロム線*/
#define PIN_NICHROME 7

#endif

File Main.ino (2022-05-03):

/*
あらかじめ，
https://github.com/askn37/Futilities
https://github.com/askn37/GPS_MTK333X
https://github.com/adafruit/Adafruit_Sensor
https://github.com/adafruit/Adafruit_BNO055
をライブラリに読み込んでおくこと．
*/


#include <Arduino.h>
#include <Wire.h>
#include <bcdtime.h>
#include <GPS_MTK333X_SoftwareSerial.h>
#include <Adafruit_Sensor.h>
#include <Adafruit_BNO055.h>
#include <utility/imumaths.h>
#include "./PinAssign.h"
#include "./Motor.h"

Adafruit_BNO055 bno = Adafruit_BNO055(55);

static int phase = 0;
/*重要！！タイマー！！ミリ秒単位で指定*/
static int Timer = 600 * 1000; //600秒 は 10分

void setup() {
    
}

void loop() {
    switch (phase)
    {
    case 0:
        Landing();
        break;
    case 1:
        GuideGPS();
        break;
    case 2:
        GuideDIST();
        break;
    case 3:
        Goal();
    }
}

/*各シークエンス*/
void Landing() {
    if (isLanded()) {
        // 前にうごかしたりパラシュート切り離したり…
    }
}

void GuideGPS() {

}

void GuideDIST() {

}

void Goal() {

}

/*Landing用*/
bool isLanded() {
    bool isLanded
    if (Timer <= millis()) {
        phase = 1;
        isLanded = true;
    } else if (isMoving()) {
        phase = 1;
        isLanded = true;
    } else {
        isLanded = false;
    }
    return isLanded;
}

/*その他*/
bool isMoving() {
    /*
    動いていたらtrue，動いていなかったらfalseを返す
    動いていないということは，すなわちスタックしている，ということではない．
    */
    const int thAccel[3] = [10, 10, 20];// 動いているかどうかの閾値設定(m/s^2)　添字0:x軸, 1:y軸，2:z軸
    bool isMoving = false;
    imu::Vector<3> Accel = bno.getVector(Adafruit_BNO055::VECTOR_ACCELEROMETER));

    if ((Accel.x() <= thAccel[0]) && (Accel.y() <= thAccel[1]) && (Accel.z() <= thAccel[2])) {
        isMoving = false;
    } else {
        isMoving = true;
    }
    return isMoving;
}

double Distance() {
    /*
    距離(cm)を返す
    一応，九軸センサー内蔵の温度センサーで温度を見て，校正しているが，だめっぽかったら15℃として計算してる
    */
    int Duration, temp = bno.getTemp();
    double Distance;
    pinMode(PIN_DIST_TRIG, OUTPUT);
    pinMode(PIN_DIST_ECHO, INPUT);

    digitalWrite(PIN_DIST_TRIG, HIGH);
    delayMicroseconds(10);
    digitalWrite(PIN_DIST_TRIG, LOW);

    Duration = pulseIn(PIN_DIST_ECHO, HIGH, 23200);//400cm以上の場合0を返す
    if (Duration > 0) {
        if (temp > 5) {
            Distance = Duration * (0.6 * temp + 331.5) / 20000;
            // D(cm) = T(μS) × 1/2(片道) × 340(m/s) × 100(cm/m) × 1/1000000(μS/S)
            // https://nobita-rx7.hatenablog.com/entry/27884818
            // D = T * 0.00005 * c(m/s) = T / 20000
            // c(近似) = 0.6 * temp + 331.5　
        } else {
            Distance = Duration / 58.8;// 15℃ 1013hpa
            // D = T * 0.017 = T / 58.8
        }
    } else {
        Distance = 400;
    }
    return Distance;
}

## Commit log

2022-05-02 Update Readme.md
    いろいろ書き足した
2022-05-03 complete Motor.h
2022-05-05 distinguish the meaning of "temperature"
2022-05-05 small fix of include
    [getGPSbeforeFlight.ino]
2022-05-05 small fix at include
    [Main.ino]
2022-05-05 add i2c addr
2022-05-06 does not work but...
    [Main.ino]
2022-05-06 ニクロム線書きました
2022-05-10 fix 4 memory saving
    [Main.ino]
2022-05-13 flight pin
2022-05-15 avoid C++ and some fix for mem
    [MotorTest.ino]
2022-05-15 make this works for fixed lib
    [MotorTest.ino]
2022-05-16 small fix of GPS
    [Main.ino]
2022-05-16 small fix for GPS
    [Main.ino]
2022-05-17 fix for software serial
    [getGPSbeforeFlight.ino]
2022-05-18 fix gps pin
2022-05-22 motor rotates well!
2022-05-22 add notes for 9 axis sensor
2022-05-25 add small tests of Flight Pin and Nichrome
2022-05-25 fix small & fatal error
    [FlightPinTest.ino]
2022-05-25 tiny fix of type
    [Main.ino, getGPSbeforeFlight.ino]
2022-06-01 try to avoid float
    [SDtest.ino, getGPSbeforeFlight.ino]
2022-06-03 ニクロム線関連
2022-06-08 fix typo, merged from dev
    [Main.ino, MotorTest.ino, SDtest.ino]
2022-06-17 fixes for real Elizabeth
    [AccelTest.ino, GuideDistTest.ino, Main.ino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]
2022-06-17 flowchart for review
2022-06-19 add flowchart
2022-06-19 huge improve at calc distance & orientation w/GPS
    [GPScalc.obj]
2022-06-28 add landing test
2022-06-28 fix for real world
    [Main.ino, getGPSbeforeFlight.ino]
2022-06-28 add/fix for 審査書
2022-07-21 draw flow and fix 4 debug
    [GuideDistTest.ino, getGPSbeforeFlight.ino]
2022-07-28 anastasis Motor
2022-07-28 update around motor
2022-07-28 trying to fix the problem
    [Main.ino, getGPSbeforeFlight.ino]
2022-08-06 add kicad data
    [DERC_CanSat_2022-B_Cu.gbl, DERC_CanSat_2022-B_Mask.gbs, DERC_CanSat_2022-B_Paste.gbp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]
